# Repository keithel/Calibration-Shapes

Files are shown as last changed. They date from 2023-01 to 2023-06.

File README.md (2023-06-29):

# Calibration Shapes

This plugin adds a menu to create some simple shapes to the scene (cube, cylinder, tube) and calibration sample parts. They are used most of the time to create some fast test parts and common calibration/test parts. 

The default size for all the simple shapes is 20 mm, but can be modified via the [**Define default size**](#Define-default-size) menu.

menu Extensions Calibration Shapes

## Calibration part

You can also load standard test  / calibration  part :

| Wiki Page | Stl Model |
|:---:|:---:|
| [Calibration Cube XYZ](https://github.com/5axes/Calibration-Shapes/wiki/Calibration-Cube-XYZ) | [Calibration Cube XYZ](./models/CalibrationCube.stl) |
| [PLA  TempTower 220 - 180°C](https://github.com/5axes/Calibration-Shapes/wiki/PLA-TempTower-220---180°C) | [PLA  TempTower 220 - 180°C](./models/TempTowerPLA.stl) |
| [PLA  TempTower 220 - 190°C](https://github.com/5axes/Calibration-Shapes/wiki/PLA-TempTower-220---190°C) | [PLA  TempTower 220 - 190°C](./models/TempTowerPLA190°C.stl) |
| [PLA+ TempTower 230 - 200°C](https://github.com/5axes/Calibration-Shapes/wiki/PLA+-TempTower-230---200°C) | [PLA+ TempTower 230 - 200°C](./models/TempTowerPLA+.stl) |
| [ABS  TempTower 250 - 210°C](https://github.com/5axes/Calibration-Shapes/wiki/ABS-TempTower-250---210°C) | [ABS  TempTower 250 - 210°C](./models/TempTowerABS.stl) |
| [PETG TempTower 260 - 230°C](https://github.com/5axes/Calibration-Shapes/wiki/PETG-TempTower-260---230°C) | [PETG TempTower 260 - 230°C](./models/TempTowerPETG.stl) |
| [PC TempTower 290 - 250°C](https://github.com/5axes/Calibration-Shapes/wiki/PC-TempTower-290---250°C) | [PC TempTower 290 - 250°C](./models/TempTowerPC.stl) |
| [Retract Tower](https://github.com/5axes/Calibration-Shapes/wiki/Retract-Tower) | [Retract Tower](./models/RetractTower.stl) |
| [Acceleration Tower](https://github.com/5axes/Calibration-Shapes/wiki/Acceleration-&-Ringing-Tower) | [Acceleration Tower](./models/AccelerationTower.stl) |
| [Layer Adhesion Test part](https://github.com/5axes/Calibration-Shapes/wiki/Layer-Adhesion) | [Layer Adhesion Test](./models/LayerAdhesion.stl) |
| [Retract Test part](https://github.com/5axes/Calibration-Shapes/wiki/Retract-Test-part) | [Retract Test part](./models/RetractTest.stl) |
| [XY Calibration Test part](https://github.com/5axes/Calibration-Shapes/wiki/XY-Calibration-Test-part) | [XY Calibration Test part](./models/xy_calibration.stl) |
| [Bridge Spiral test](https://github.com/5axes/Calibration-Shapes/wiki/Bridge-Spiral-test) | [Bridge Spiral test](./models/BridgeTest.stl) |
| [Thin Wall Test](https://github.com/5axes/Calibration-Shapes/wiki/Thin-Wall-Test) | [Thin Wall Test](./models/ThinWall.stl) |
| [Overhang Test](https://github.com/5axes/Calibration-Shapes/wiki/Overhang-Test) | [Overhang Test](./models/Overhang.stl) |
| [Flow Test](https://github.com/5axes/Calibration-Shapes/wiki/Flow-Test) | [Flow Test](./models/FlowTest.stl) |
| [MaxFlow Test](https://github.com/5axes/Calibration-Shapes/wiki/MaxFlow-Test) | [MaxFlow Test](./models/MaxFlow.stl) |
| [Tower Flow Test](https://github.com/5axes/Calibration-Shapes/wiki/FlowTower-Test) | [TowerFlow Test](./models/Flow-tower-04x02.stl) |
| [Hole Test](https://github.com/5axes/Calibration-Shapes/wiki/Hole-Test) | [Hole Test](./models/HoleTest.stl) |
| [BackLash Test](https://github.com/5axes/Calibration-Shapes/wiki/BackLash-Test) | [BackLash Test](./models/Backlash.stl) |
| [Linear/Pressure Advance Tower](https://github.com/5axes/Calibration-Shapes/wiki/Linear-Pressure-Advance-Tower) | [Linear/Pressure Adv Tower](./models/PressureAdvTower.stl) |
| [Junction Deviation Tower](https://github.com/5axes/Calibration-Shapes/wiki/Junction-Deviation-Tower) | [Junction Deviation Tower](./models/JunctionDeviationTower.stl) |
| [Tolerance Test](https://github.com/5axes/Calibration-Shapes/wiki/Tolerance) | [Tolerance Test](./models/Tolerance.stl) |
| [Support Test](https://github.com/5axes/Calibration-Shapes/wiki/Support-Test) | [Support Test](./models/SupportTest.stl) |
| [Lithophane Test](https://github.com/5axes/Calibration-Shapes/wiki/Lithophane-Test) | [Lithophane Test](./models/Lithophane.stl) |
| [Dimensional Accuracy Test](https://github.com/5axes/Calibration-Shapes/wiki/Dimensional-Accuracy-Test) | [Dimensional Accuracy](./models/DimensionalAccuracyTest.stl) |
| [MultiCube Test](https://github.com/5axes/Calibration-Shapes/wiki/MultiCube) | [MultiCube Test](./models/MultiCube.stl) |

Multi flow parts : For this parts the initial design is scaled to the nozzle size

| Wiki Page | Stl Model |
|:---:|:---:|
| [Parametric Multi Flow test](https://github.com/5axes/Calibration-Shapes/wiki/MultiFlowTest) | [Flow 100%](./models/Flow100.stl) |

Bed Level : For this part the initial design is scaled to the bed size

| Wiki Page | Stl Model |
|:---:|:---:|
| [Parametric Bed Level Calibration](https://github.com/5axes/Calibration-Shapes/wiki/ParametricBedLevel) | [Bed Level Calibration](./models/ParametricBedLevel.stl) |

Multi-Extruder Calibration part

- [Cube bi-color](https://github.com/5axes/Calibration-Shapes/wiki/Cube-Bi-Color)
- [Calibration Cube bi-color](https://github.com/5axes/Calibration-Shapes/wiki/CubeCalibrationBiColor)
- [Extruder Offset Calibration](https://github.com/5axes/Calibration-Shapes/wiki/ExtruderOffsetCalibration)

All the parts have been designed via OpenSCAD. OpenSCAD can be downloaded [here](http://www.openscad.org/downloads.html)

### Define default size

The function **Define default size** gives you the possibility to change the default size for the standard primitives (cube/cylinder/tube).

define default size

This plugin is using the [Trimesh](https://github.com/mikedh/trimesh) library to create [simple shapes](https://github.com/mikedh/trimesh/blob/master/trimesh/creation.py) and to load STL files.

## Cura-Postprocessing-Scripts

Several postprocessing Scripts are included into the plugin to help the user to generate automaticaly the differents Towers.

- [RetractTower.py](./resources/scripts/RetractTower.py)
- [SpeedTower.py](./resources/scripts/SpeedTower.py)
- [TempFanTower.py](./resources/scripts/TempFanTower.py)
- [FlowTower.py](./resources/scripts/FlowTower.py)
- [MaxFlow.py](./resources/scripts/MaxFlow.py)

### Copy Scripts

These scripts can be copied into the scripts directory via the function **Copy Scripts**.

**Note :** Since Cura 4.9 you don't need to use this function anymore. Has been removed from the menu.

**After you have copied these scripts, you must restart Cura to see the scripts in the postprocessing scripts list.**

### Tower generation scripts
The scripts provided with this plugin must be visible in the Postprocessing scripts list.

Adding script

#### [SpeedTower.py](resources/scripts/SpeedTower.py)

Description :  postprocessing-script to easily define a Speed Tower.

Five options :

    - Jerk   :  Speed variation (M204 S) 
	
    - Acceleration :  Acceleration variation (M205 X Y) 
    
    - Junction Deviation :  Junction Deviation variation (M205 J) 
    
    - Marlin Linear  :  Marlin Linear Advance (M900 K)

    - RepRap Pressure  : RepRap Pressure Advance (M572 D0 S)

SpeedTower.py

#### [TempFanTower.py](resources/scripts/TempFanTower.py)

Description:  postprocessing-script to easily create a temptower and not use 10 changeAtZ-scripts

 The default values are for this temptower PLA model : [PLA TempTower 220°C - 180°C](./models/TempTowerPLA.stl)
- Temp Tower PLA from 220°C to 180°C  (Other design possible to test PLA from 220°C to 190°C)
- Possibility to define also a Fan Tower , Fan percentage speed are defined with semi-colon as separator in the fan variation field

TempFanTower.py

#### [RetractTower.py](resources/scripts/RetractTower.py)

Description:  postprocessing-script to easily create a Retract Tower

The default values are for this Retract Tower model : [Retract Tower](./models/RetractTower.stl)
 
Two options :

    - Speed   :  Speed variation
	
    - Retract :  Distance retract variation

RetractTower.py

#### [FlowTower.py](resources/scripts/FlowTower.py)

Description:  postprocessing-script to easily create a FlowTower

 The default values are for this FlowTower model : [FlowTower Nozzle 0.4 / Layer height 0.2](./models/Flow-tower-04x02.stl)
- FlowTower from 110% to 90% 
    - Using Flow Varation   :  [Flow Varation](https://marlinfw.org/docs/gcode/M221.html) (M221 S) 

FlowTower.py

#### [MaxFlow.py](resources/scripts/MaxFlow.py)

Description:  postprocessing-script to easily create a test for the Maximum speed of the Printer.

 The default values are for this FlowTower model : [MaxFlow Test](./models/MaxFlow.stl)
- Max Flow Test from 50% to 150% 
    - Using Speed Varation   :  [Speed Variation](https://marlinfw.org/docs/gcode/M220.html) (M220 S) 

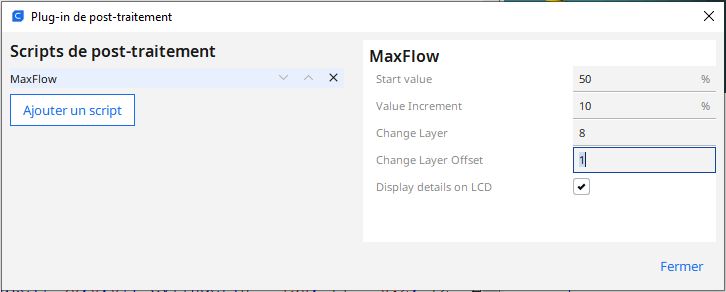
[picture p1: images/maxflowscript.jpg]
MaxFlow.py


## Add Mark

This function has been removed from the last versions and is now the subject of a specific plugin with many more possibilities. You can find the plugin at the following address: [Name It!](https://github.com/5axes/NameIt))

## Help

This function will redirect you on the [Wiki](https://github.com/5axes/Calibration-Shapes/wiki) of this repositery.

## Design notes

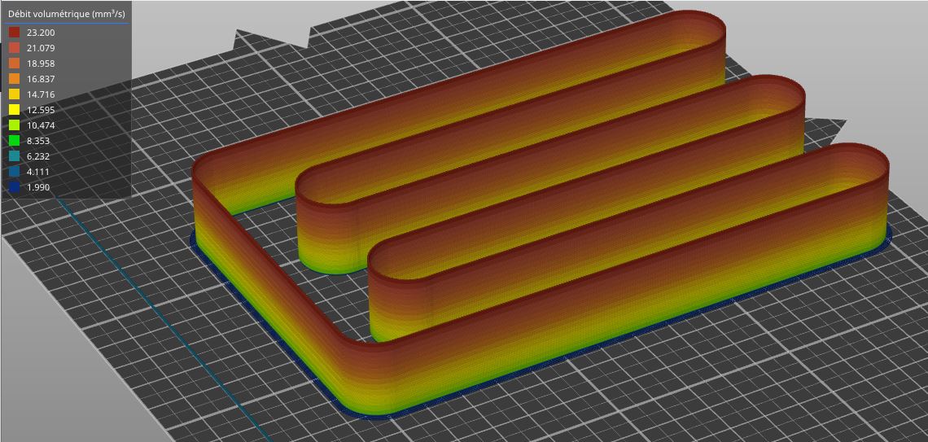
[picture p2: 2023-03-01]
images/MaxFlow.jpg

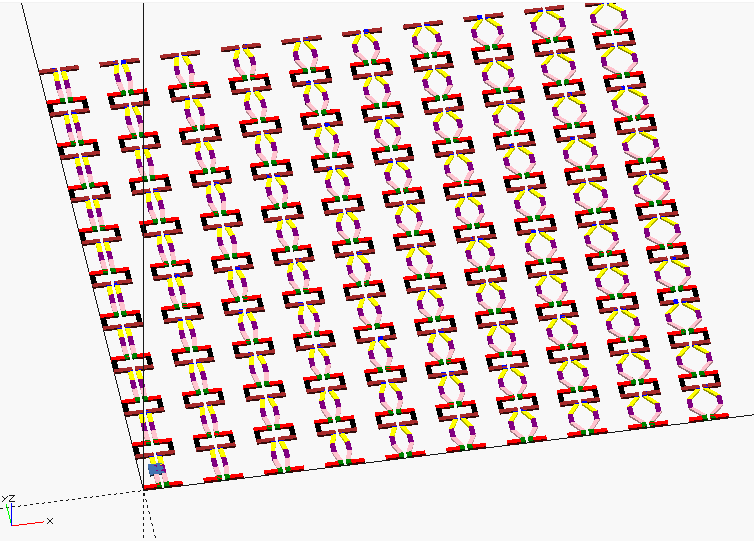
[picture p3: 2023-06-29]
images/Backlash.png

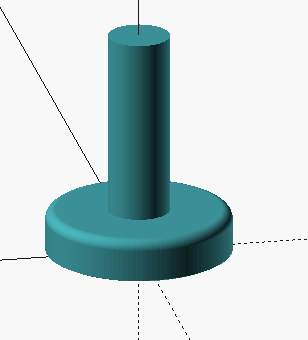
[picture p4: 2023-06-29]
images/LayerAdhesion.png

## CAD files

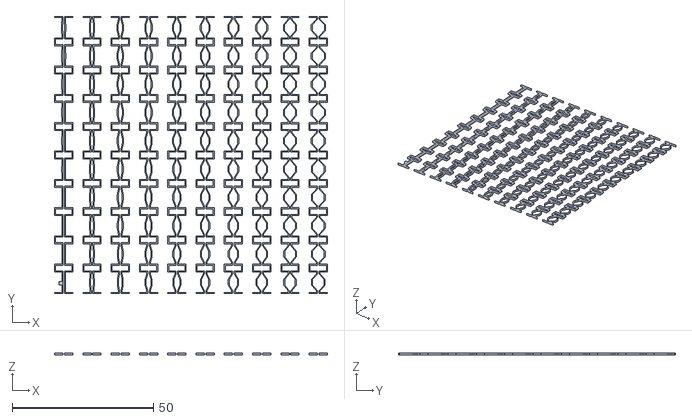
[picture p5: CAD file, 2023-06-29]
models/Backlash.stl
96.5 x 98.0 x 0.8

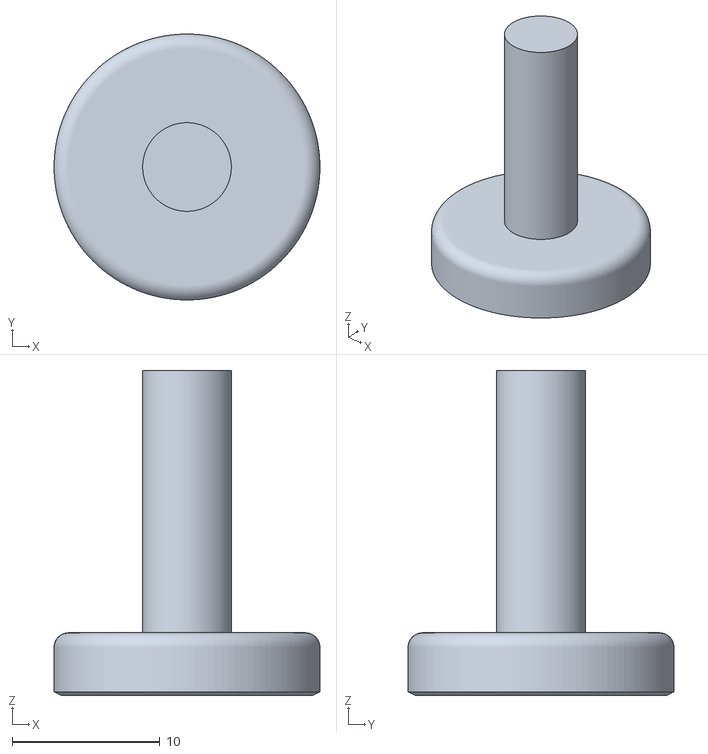
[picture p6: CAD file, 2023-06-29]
models/LayerAdhesion.stl
18.0 x 18.0 x 22.0

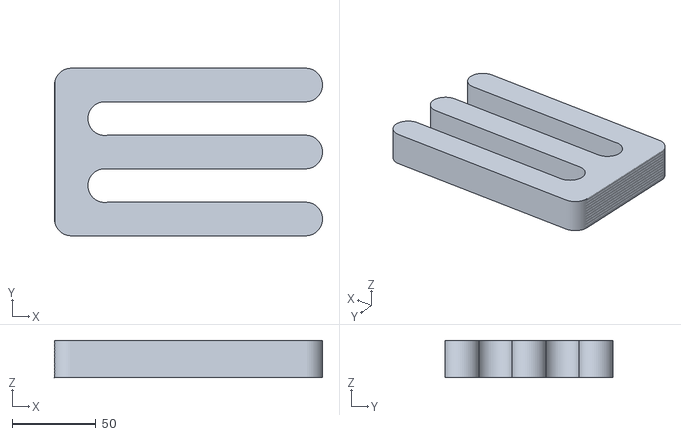
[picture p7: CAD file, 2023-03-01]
models/MaxFlow.stl
160.0 x 100.1 x 22.2

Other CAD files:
models/Backlash.scad
models/LayerAdhesion.scad
models/MaxFlow.scad

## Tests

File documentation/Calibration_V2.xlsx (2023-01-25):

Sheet: Utilisation
Test de précision de l'imprimante 3D
Date | 2021-11-11
Imprimante | Ender-3
Version Cura | Ultimaker Cura 4.12
Step calibrées ? | Oui
Température au moment de l'impression (il s'agit approximativement de la température du lit d'impression) | 60 | °C
Température lors de la mesure (température ambiante) | 20 | °C
coeficient of thermal expansion | 68 | µm/mmK | (ABS: 90, PLA: 68, PETG: 60)
 |  |  | https://www.simplify3d.com/support/materials-guide/properties-table/
 |  |  | attendu
 |  | maintenant | après correction | Code pour mise à jour | Pour sauver: | M500
Réglage de l'axe X [pas par mm] |  | 80 | 79.81 | M92 X79.809
Réglage de l'axe Y [pas par mm] |  | 80 | 79.77 | M92 Y79.769
Réglage de l'axe Z [pas par mm] |  | 400 | 399.43 | M92 Z399.545
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

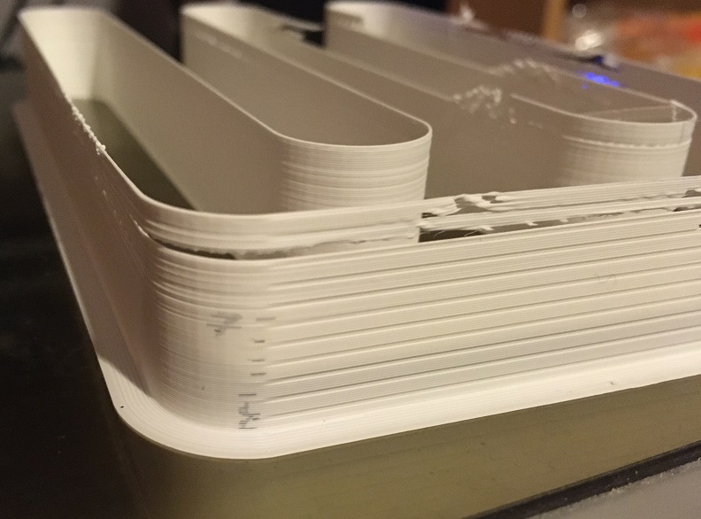
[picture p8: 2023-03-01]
images_result/MaxFlowDetail.jpg

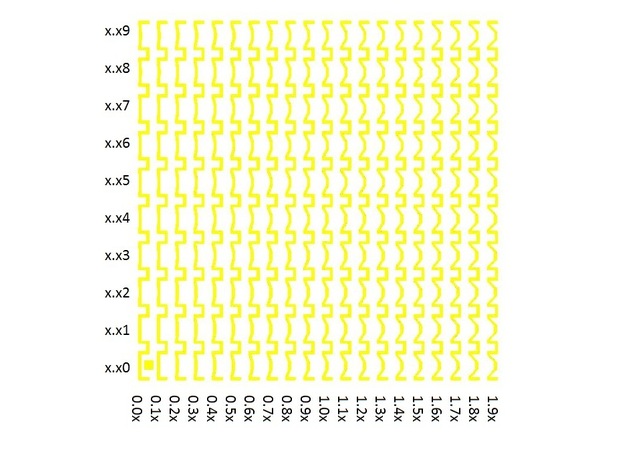
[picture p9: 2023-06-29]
images_result/backlash1.jpg

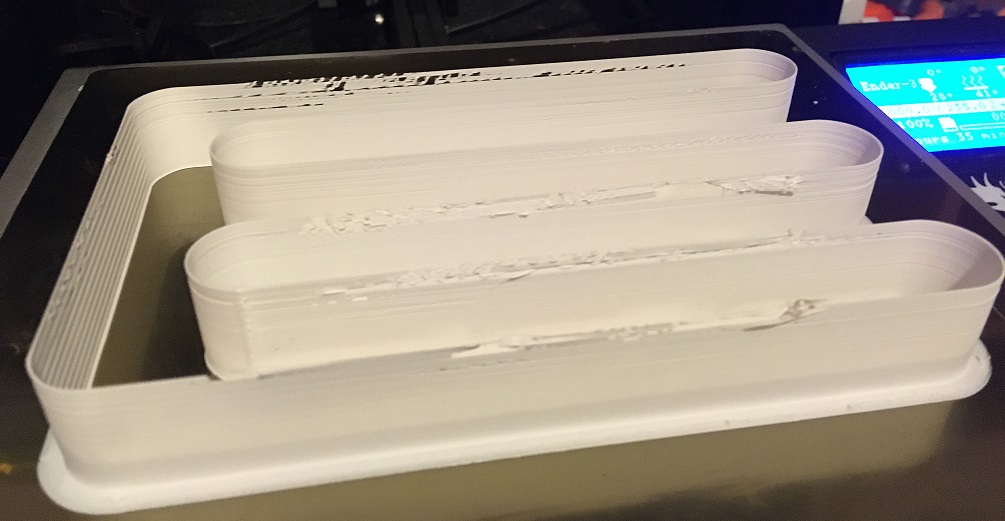
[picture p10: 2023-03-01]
images_result/MaxFlowGlobal.jpg

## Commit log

2023-01-25 Test trad (#131)
    * prepare French translation
    * update
    * Update i18n template
    * Update CalibrationShapes.py
    * Update i18n template
    * update
    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
    [Calibration_V2.xlsx]
2023-02-27 V2.2.2
    Add Max Flow Speed
    [MaxFlow.scad, MaxFlow.stl]
2023-02-27 Update Design
    [MaxFlow.scad, MaxFlow.stl]
2023-02-27 Update Image
    [MaxFlow.stl]
2023-03-01 update script defaut value
    [MaxFlow.scad]
2023-03-01 Change Design MaxFlow
    Add LAyer 1 for Speed 100%
    [MaxFlow.scad, MaxFlow.stl]
2023-03-01 change origine
    [MaxFlow.scad, MaxFlow.stl]
2023-06-29 V2.2.5
    LayerAdhesion
    [LayerAdhesion.stl]
2023-06-29 update model
    [Backlash.scad]
